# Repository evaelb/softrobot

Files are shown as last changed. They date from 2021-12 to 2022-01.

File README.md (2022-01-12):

# Soft Robot Gripper
One-week project: building a soft robot gripper

# About the Project
Soft robotics is a subfield of robotics that concerns the design, control, and fabrication of robots composed of compliant materials, instead of rigid links. In contrast to rigid-bodied robots built from metals, ceramics and hard plastics, the compliance of soft robots can improve their safety when working in close contact with humans. It is inspired by soft-bodied animals and permits adaptive, flexible interactions with unpredictable environments.

In our project we wanted to build a soft robotic gripper, that would lift up fragile objects gently and without breaking them.

Here we will describe our one week long project.



# Idea and Design
The initial idea of our project was to build a soft robot gripper, with a feedback system. The grippers we considered had four or three fingers. We educated ourselves on benchmark and former projects e.g. on the soft robotics toolkit. https://softroboticstoolkit.com/
Also we initially planned to include a sensor or feedback system, which is explanatory for certain design choices we took afterwards.

Each arm, was supposed to be independent, and to bend in the same way, in the same time, to be able to catch an object softly but with enough power. 
The sensor feedback system was also suppposed to fulfil two tasks: Indicate the position of each arm at each given time, and also to be able to sense pressure or/and presence/contact with object.
To do so, we had several development process ideas, but not enough time to invest in them, the following part was already enough. To develop the skills required to master the silicon molding required us full 3 days.

# Mold design and development
The design and simulation part was initially planned to be done with SOFA, https://www.sofa-framework.org/, with a plugin for soft robots. But again to be able to master and use it, we would have needed 3 or 4 full days, wich was not possible for us.

The mold design was finally done with the Fusion 360 Software. The model was the printed out with a laser cutter on an acrylic plate.
In our first molds we first created a mold with an air channel and then one without air channel. The middle part (negative part of the air chambers) were glued onto the middle part first, to not create slits in which the silicone could go into. The other parts were glued together with a hot glue gun.
We first tested every mold with water, to test if it would leak. According to that we taped the molds from underneath to prevent the silicone to leak. 
The molds were then filled with silicone. The silicone was mixed by two liquid silicones that would dry out in around 40 minutes.

This type of mold, required 2 steps to build the complete soft robots. It has 2 major issues. First, the merging edges are very often not completely impermeable, a lot of leakage has to be fixed, and the internal structure of the air canals very often not destroyed or altered the air-channel design. Second of all, and most important point we learned, is that this 2 steps technique does not allow to control efficiently the thickness of the walls around the air canals. But this ratio betwenn the thickness/ or resistance to elongation by the air pression, is the key to control precisely the direction, flexibility, and shape of the movement done by each arm. 

We then kept the same design, but changed the mold in a way to be build the soft robots in one step.
And is we were expecting, this last version, was also the best.

# Setup
The Gripper consists of a silicone model with air channels which are stacked into a air pumping system, with a wall very thin and the opposite thicker. The Air pumping system is composed of 3 relays, controled by an arduino board, 3 valve, allowing the air pumped by 2 motors to go or not into the 3 separted air canals of the robots.


# Code
The code used for the arduino can be downloaded through this link or can be downloaded directly from this repository as well (folder 'AirPumpRelay2'). 

# DFX Files
There is 3 files. The base (base x1+ wall (and the little connectors x9 each the long wall x6) the air canal line has to be engraved, to give indication of were putting the air canal afterward.
The air canal, wich have to be add on top of one layer of the connectors. Wich allow him to be at 0.5 cm above the base.
The central module, wich is the only hard material used in the final soft robots, to allow the air tube to come into the robot, and to fix the junction of the 3 arms (the robot for movement need a solid piece to hold at).
The holes have to be closed afterward with silicon and 3 tubes of the correct size have to be added on the beginning of the air canals, to make place for the entry of the future air tubes of the pumping system.

Finally the connectors are glued with an special super strong acrylic glue, and the others are just assembled together. The impermeablility of the mold / to stop moving part to move, a little bit of normal hot glue is applied to each possible leakage joints.

For the de-molding the best is to take out each moving part, by destroying the connections made by the hot glue, and by taking out very carefully step by step the air canal by sliding it in the arms direction, outward. It requires to twist a bit the silicon, but thanks to its elasticity no issues.





# Challenges

Firstly, the modeling software was quite complex and time-intense. Other challenges were to control the thickness of the silicone layers to control the inflation movement of the silicone model. One option to solve this would be to 3D-print the flexible parts of the gripper directly, as it gives more control than with our model. 
Concerning the pumping system it was challenging to get enouch air-pressure to inflate our silicone model. As we only had two air-pumps for three canals, we created a system that would pump three canals with two-pumps. Still every canal can be controlled individually with the valves connected to the arduino.

Another challenge is to get some kind of feedback system that reports on the stage of the gripper (inflated/deflated) and / or a sensor system that tells if the gripper is touching something. Herefor we considered a contact sensor containing liquid or a flexible tissue sensor. This system would have to be integrated parallel to the air-canal system. However, due to the lack of resources and timely constraints we did not implement a sensor/feedback system. 

# Further information
Please to repeat the experience and benefits of our expererience and error made, feel free to contact via git.

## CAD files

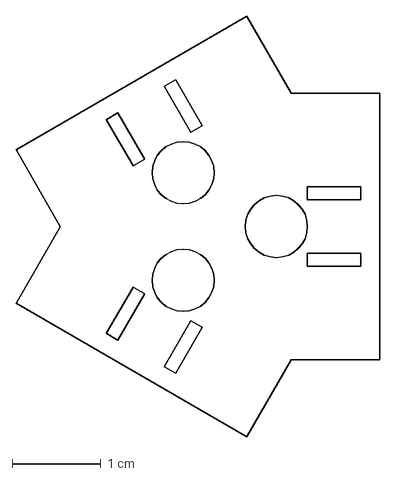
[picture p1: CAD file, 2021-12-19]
Central_module.dxf
4.10 x 4.73 cm

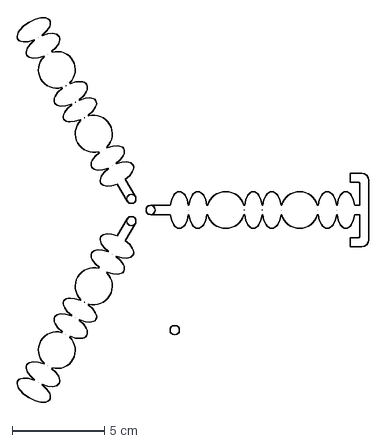
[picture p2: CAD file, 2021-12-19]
Convex Canal.dxf
19.1 x 20.9 cm

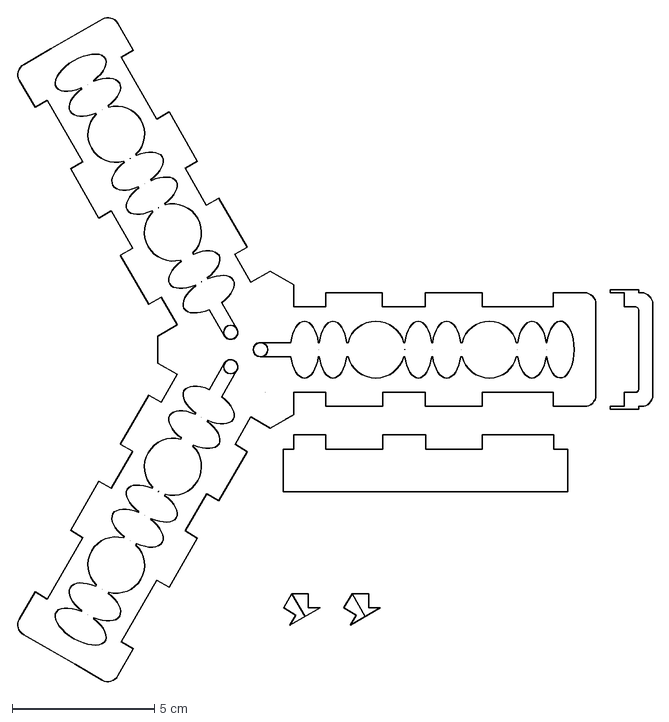
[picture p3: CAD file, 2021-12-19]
Base.dxf
22.4 x 23.4 cm

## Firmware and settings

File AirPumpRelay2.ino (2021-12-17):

int Relay1State = LOW;
int Relay2State = LOW;
int Relay3State = LOW;
long StartTime = 0; 


const long interval = 3000;  

const int RelayPin1 =  3;
const int RelayPin2 =  4;
const int RelayPin3 =  5;

void setup() {
  // put your setup code here, to run once:
pinMode(RelayPin1, OUTPUT);
pinMode(RelayPin2, OUTPUT);
pinMode(RelayPin3, OUTPUT);

}

void loop() {

unsigned long CheckTime = millis();

unsigned long elapsedTime = CheckTime - StartTime;

if(elapsedTime > interval) {

  StartTime = CheckTime;   

  }

if (elapsedTime < 2500){

  Relay1State = HIGH;  
  Relay2State = HIGH; 
  Relay3State = HIGH;               

  }
if (elapsedTime > 2500){

  Relay1State = LOW;
  Relay2State = LOW;
  Relay3State = LOW;
                  

  }

  
digitalWrite(RelayPin1, Relay1State);
digitalWrite(RelayPin2, Relay2State);
digitalWrite(RelayPin3, Relay3State);

}
